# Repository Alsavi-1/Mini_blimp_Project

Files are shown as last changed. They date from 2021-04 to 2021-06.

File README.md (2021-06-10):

# Mini_blimp_Project
ECE412/ECE413 PSU Capstone 2021
CoppeliaSim 
  - Blimp simulation file
  - Tutorial for CppeliaSim itself
Main Document
  * 412 Document
    - Research/work done during (Winter term 2021)
  * 413 Document
    - Research/work done during (Sprin term 2021)
  * Full BOM Assembly
    - 3D solid works part for Gondola
    - Contains materials to build gondola
  * Full Blimp Analysis
    - 3D solid works part for Gondola
    - Contains materials to build gondola
  - 
  -
  -
  -
  -
Meeting minutes
  - Thursday Meetings with Ethan
Research Readings
  - Research papers involving blimps
    - Not used Papers (Research papers that weren't applicable)
    - Used Papers (Applicable information involving blimps)
WPR (Weekly Progress Reports)
  - Each date contains the current work done that week and what is going to be done the next

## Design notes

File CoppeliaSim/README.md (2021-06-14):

The simulation file in this directory was developed with CoppeliaSim V4.1.0 (rev. 1).\
The current version of CoppeliaSim (as of the submission of this project) is V4.2.0 (rev. 5).\
Previous versions of CoppeliaSim may be found at:\
   https://www.coppeliarobotics.com/previousVersions

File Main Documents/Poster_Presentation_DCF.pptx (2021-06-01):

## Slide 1

Development of an Autonomous Blimp

Ben Vu, Dylan Filkins, Jacob Thomas, Nick Short, Victor Albarran, Zeming Zhou

Portland State University and Galois Inc

INTRODUCTION:

The growing applications of unmanned aerial vehicles (UAV) allows for cross industry benefits. One such UAV that could see large potential in these industries are blimps. These light than air vehicles provide a large range of capabilities due to their stability and energy consumption.
Galois Inc. proposed a project in which they could use a blimp within their office environment to relay messages to coworkers and have messages forwarded. Galois Inc. saw this a benefit to communicating in the office environment in an entertaining manner.
The joint venture between the electrical and mechanical engineering departments at Portland State University collaborated to develop a simulated blimp to iteratively analyze computer aided design (CAD) models. The design process was to look at different use cases for Galois Inc. and to determine the best configuration.
*Due to the COVID-19 pandemic, the scope and possibility of constructing a physical prototype was not possible.

OBJECTIVE:

software uses a 3D model of the blimp in addition to statistics about the blimp such as mass, buoyancy and maximum thrust to simulate the blimp moving within 3D space.
Navigation proved to be particularly difficult due to the lack of wheels or airfoils binding the velocity and heading of the blimp together. Instead, other methods were employed to recreate the forces normally provided by those features.
By oversteering through the turn, the thrust of the blimp can be used to redirect the velocity of the blimp to follow the desired curve.

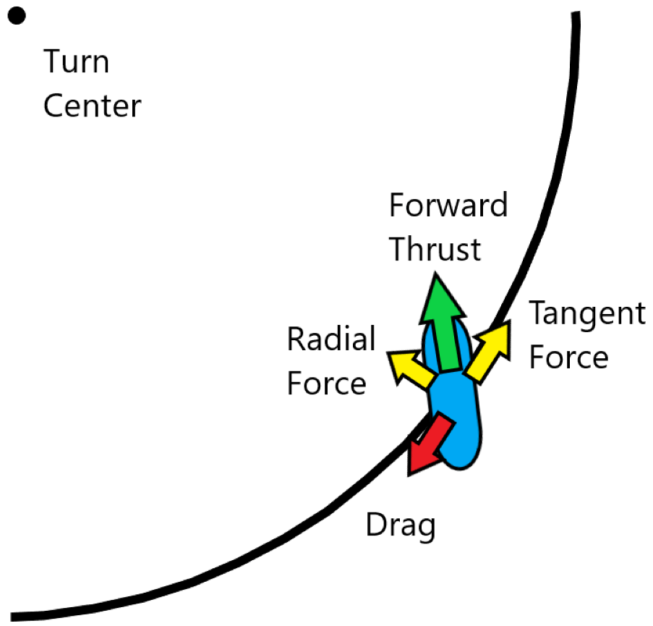
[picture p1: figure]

Chassis:
As part of a valuable deliverable for the sponsor a CAD design was developed to be used together with simulations. The basis of this was to be efficient with the limited time that the capstone had to evolve the simulation and design. Additionally, the simulation could provide more insights into how the chassis design would interact with the surrounding environment.
Only one chassis design was implemented due difficulties with the COVID-19 pandemic and sponsor’s interest

The chassis and the full-scale model is illustrated below in Figure 1 & 2. The CAD design was evaluated for pressure and velocity drop across the system ( Figure 3 & 4).

consideration the defined criteria of Galois Inc. in regards to modularity, manufacturability, and protection of electrical components.
It is suggested that future evolutions are made with the combination of simulations and CAD to further refine the project. All deliverables and documentation was passed onto Galois Inc. to provide a foundation of knowledge for the next version.

REFERENCES:

- Tao, Qiuyang & Tan, Tun & Cha, Jaeseok & Yuan, Ye & Zhang, Fumin. (2020). Modeling and Control of Swing Oscillation of Underactuated Indoor Miniature Autonomous Blimps. Unmanned Systems. 09. 10.1142/S2301385021500060.
- Jinjun Rao, et al. “A Flight Control and Navigation System of a Small Size Unmanned Airship.” IEEE International Conference Mechatronics and Automation, 2005, July 2005, doi:10.1109/icma.2005.1626776.
- Zufferey, Jean Christophe et al. “Flying over the Reality Gap: From Simulated to Real Indoor Airships.” Autonomous Robots 21.3 (2006): 243–254. Autonomous Robots. Web.
- Zheng, Zewei, Huo, Wei, & Wu, Zhe. (2013). Autonomous airship path following control: Theory and experiments. Control Engineering Practice, 21(6), 769–788.
- Ko, Jonathan et al. “Gaussian Processes and Reinforcement Learning for Identification and Control of an Autonomous Blimp.” Proceedings - IEEE International Conference on Robotics and Automation. N.p., 2007. 742–747. Proceedings - IEEE International Conference on Robotics and Automation. Web.
- Alsayed, Ahmad, and Eric Lanteigne. “Experimental Pitch Control of an Unmanned Airship with Sliding Ballast.” 2017 International Conference on Unmanned Aircraft Systems (ICUAS), 2017, doi:10.1109/icuas.2017.7991326.

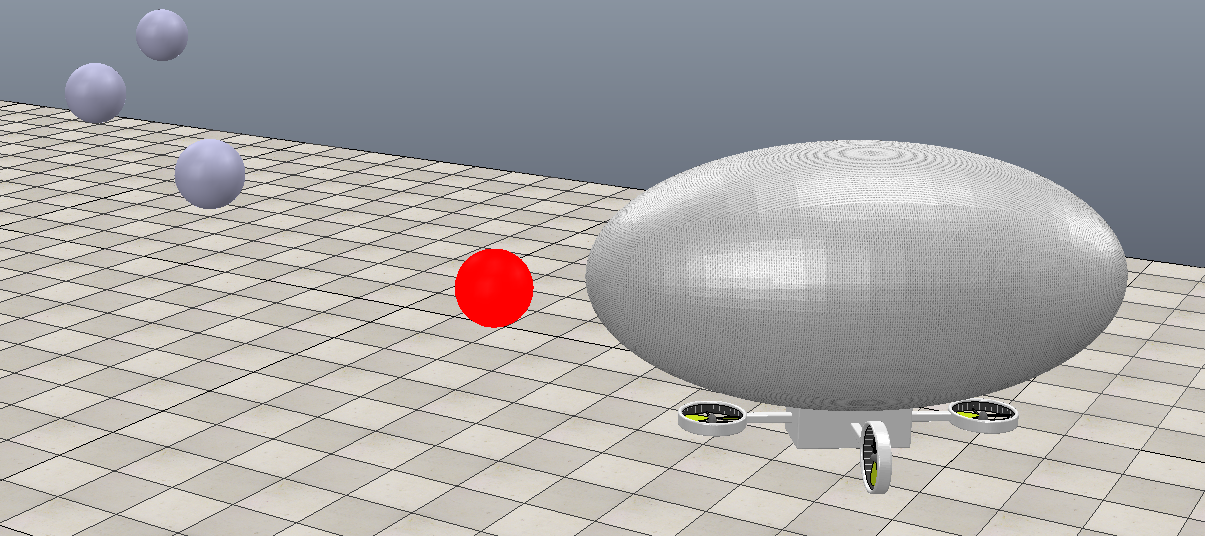
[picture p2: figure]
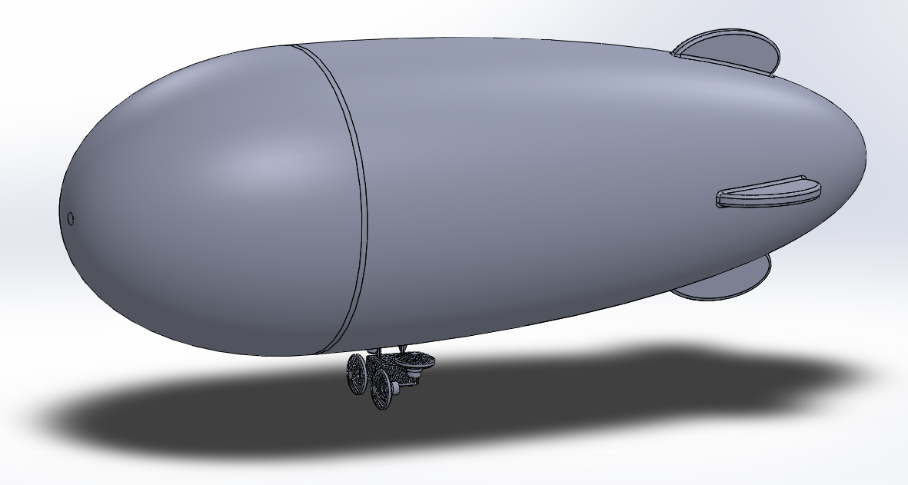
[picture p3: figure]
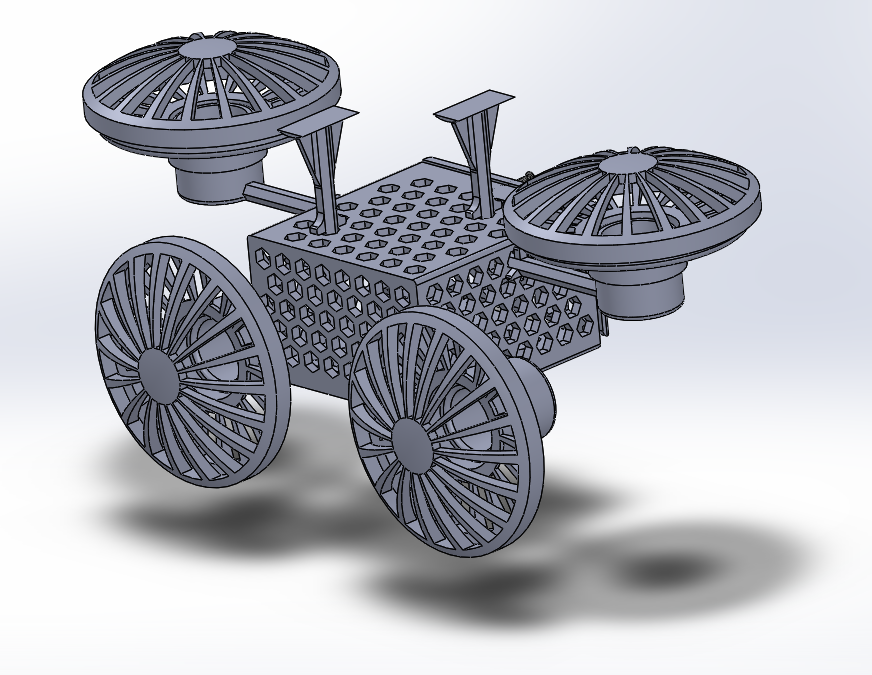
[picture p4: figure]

Figure 1: Full scale CAD model (left) and Figure 2: chassis design (right)

Figure 3 and 4: Illustrating aerodynamics of CAD model in regards to velocity and pressure changes.

CONCLUSIONS:

The pass off of knowledge and deliverables were completed to Galoic Inc. and Portland State University to a satisfactory level. The team was able to successfully develop several simulations in the programs of CopelliaSim and WeBots to start to look at different use cases for the sponsor. Within these simulations, we were able to model a blimp to follow a path of different waypoints and to define the outside factors affecting the blimps directional path.
A refined three dimensional CAD model was produced for these simulations to see the interactions. The model considered different engineering analysis of strength, material, and aerodynamics that could affect life cycle of the chassis. The CAD model also took into consideration the defined criteria of Galois Inc. in regards to modularity, manufacturability, and protection of electrical components. he CAD model also took into

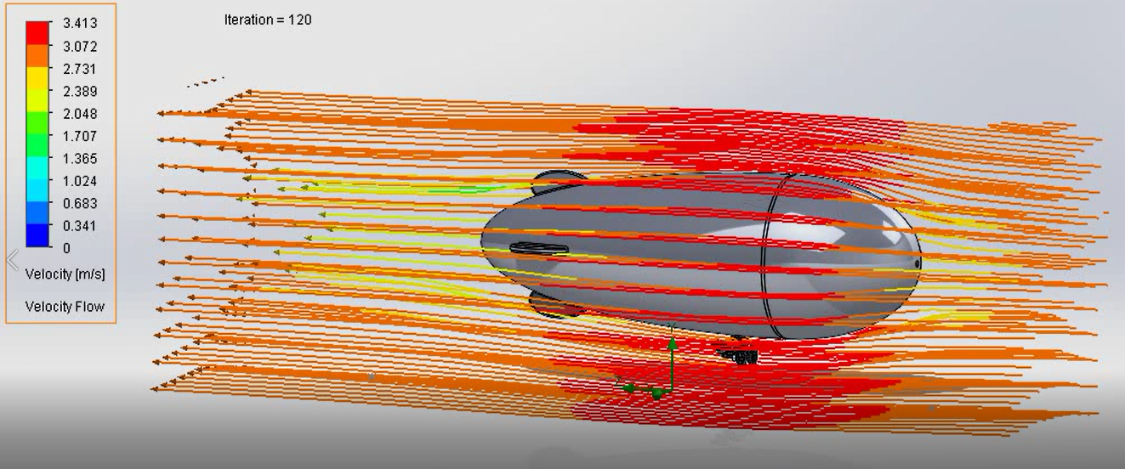
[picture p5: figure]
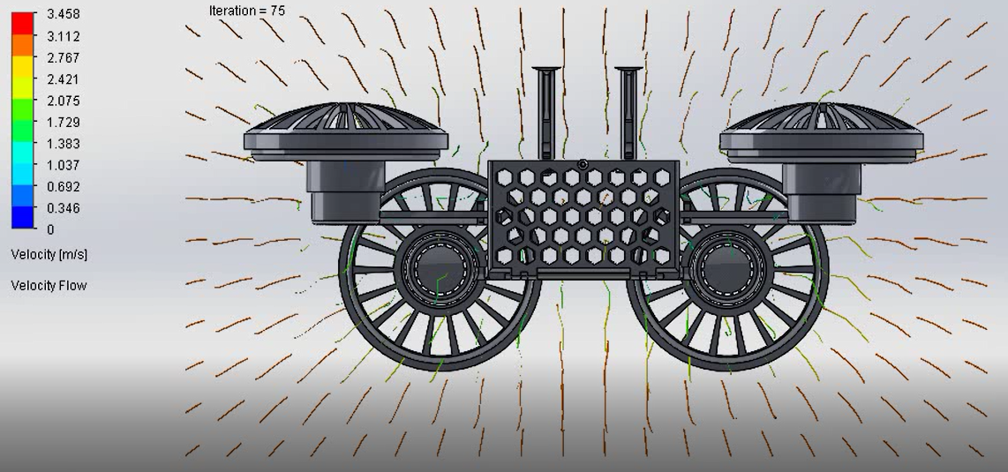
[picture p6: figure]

Create a simulation of a blimp and use the simulation to learn how blimps move, and create a chassis which can be used as a blimp gondola.

RESULTS:

Simulations:
Because meeting in person was not an option, a physics simulation was employed to model the dynamics of a blimp. This gave the opportunity to visualise blimp movement and investigate navigation methods. Two softwares were used: CoppeliaSim and WeBots. Each

ACKNOWLEDGEMENTS:

Special thanks for Galois Inc for sponsoring the capstone project and furthering our education through their support and dedication.
We thank professor Dr. Mark Faust for the constant assistance throughout the capstone project as well, as the electrical engineering insights to further develop our project.
We are appreciative for Dr. Marek Perkowski and Dr. Jun Jiao for their commitment in propelling our understanding of engineering topics. Through their inquisitive questions and presenting subject matter.

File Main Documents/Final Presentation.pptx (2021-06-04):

## Autonomous Mini Blimp

Team 4:
Ben Vu, Dylan Filkins, Jacob Thomas, Nick Short, Victor Albarran, Zeming Zhou
Sponsor: Galois Advisor: Marek Perkowski

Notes: Hello, this is team 4’s autonomous mini blimp project
Our sponsor is Golois and advisor is Dr. Perkowski
I’m Ben

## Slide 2

## Concept of Operations

Initial task
- Create a mini-blimp with some autonomous controls
- Is able to be manually controlled (similar to RC flight) by user
Now the task is to find simulation software that can validate blimp design
- Test different blimp designs (Volume, Shape, # of propellers)
- Simulate blimp performance
- Be able to output speed and turning capabilities of blimp

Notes: Original Concept of Operations
1 Concept of Operations
The purpose of this project is to design a proof of concept of a semi-autonomous blimp
that will fly around an office space which is our Minimum Viable Product (MVP). The
craft uses helium as its primary lift mechanism, the craft must be remotely operable by a
typical hobby controller, and all power sources, radios, sensor control systems are
subject to a weight restriction depending on the blimp helium and shape. Manual control
from a remote will allow the user six-degrees of freedom. Galois will use the final
designed blimp to be used in an office environment for various tasks and for a team
competition between blimps.

Ben 1

At the start, the idea was to create a mini-blimp with some autonomous controls
Which would be collision detection
But for the most part is user controlled with a hobby controller
That was a big promise and would prove to go beyond 2 terms
Now we revised the plan to use a simulation software to validate blimp design
The software will be able to test various designs (such as, size, shape, # of propellers)
And that will be used to simulate its performance
Then outputs its speed and turning capabilities

## Initial Plan

- The initial plan was to develop an autonomous blimp prototype for two scenarios (office use for Galois and DARPA competition).
- The office environment would be to relay information and messages to employees.
- The DARPA competition required the blimp to perform in a Quidditch like match to showcase capabilities
- Considerations by Galois and DARPA would be considered for autonomous operating and outside influences (wind, image recognition, attacks, etc)

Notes: Dylan:

As mentioned earlier

## Revised Plan

- Due to COVID-19 impacts the scope of the project was changed to focus efforts on office use.
- AI would be integrated later by the sponsor
- Creating a physical prototype was determined to be unfeasible. Instead a computer simulation would be created
- The simulation would model the behavior of a blimp to provide information about blimp dynamics
- The simulation could then be used to help design a custom chassis

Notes: Jacob 1

## The Main Components of the Blimp

- Envelope - It consists of a shell containing a gas less dense than air. The gas not only provides lift for the airship, but also provides a "structure" for the envelope to keep the shape of the shell unchanged.
- Gondola - It is used to carry various electronic equipment and as the connection point of the engine. The gondola is the heaviest part of the airship, so the lightest materials must be selected to manufacture the gondola.

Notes: zeming:

## Diagram

- Chassis Specifications:
  - ~ 22 x 10 x 8.5 cm
  - 80 grams without components
  - PLA
- Chassis Considerations:
  - Airflow over electrical components
  - Shroud over propellers
  - Protection of electrical components
  - Modularity in propeller placement

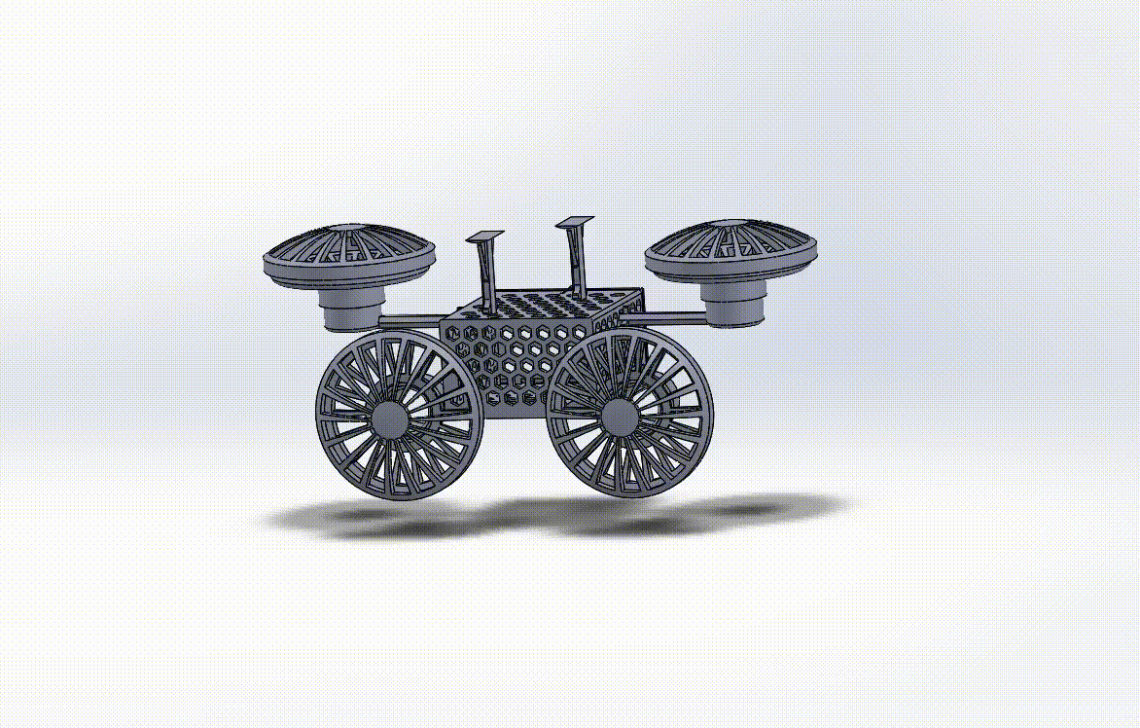
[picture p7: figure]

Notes: Dylan 2:

The diagram was an additional deliverable that was to be implemented along with the simulation. This was to allow concurrent development of the design and simulation. This allowed a proper efficiency of time and gain greater insight into the effect of the chassis design.

So you can see the design in the full scale with a respective size of 1.4 m. If we look at the two photos below, we will see the chassis design that was design. As well as the exploded view of the design with all fasteners.

The chassis design was further analyzed with the material properties and looking at the sponsor’s desires.

## Overview of Software

- Several softwares were considered for use
- Each software was ranked based on features which were considered to be important
  - Physics Modeling
  - Ability to calculate path deviation
  - Ability to visualize simulation
- Two softwares were chosen to create simulations:

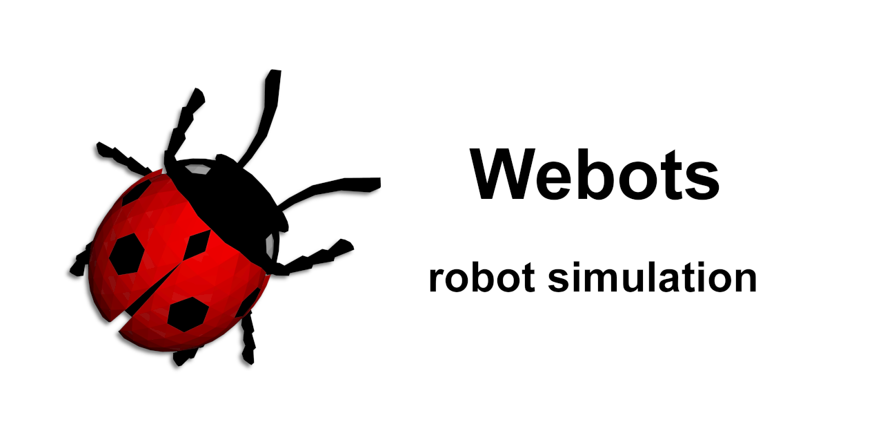
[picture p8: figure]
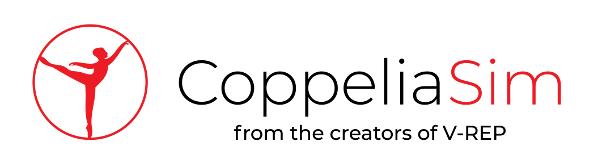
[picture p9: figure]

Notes: Jacob 2

## CoppelliaSim

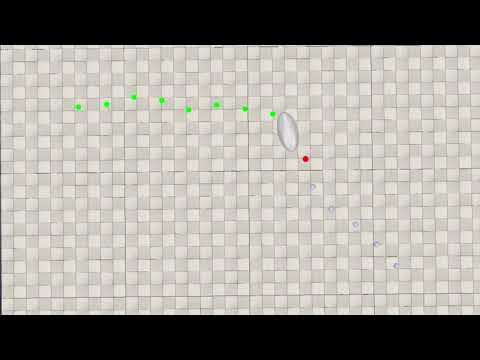
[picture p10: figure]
CoppeliaSim Simulation of a blimp with primitive way point navigation.

- Open source and multi-platform desktop application
- Built-in library includes robots, sensors, and actuators.
- Simulation scripts are natively written in LUA.
- Remote API access via C++, Java, Python, Matlab, and LUA.
- Several options for physics engines, including Bullet, ODE, Vortex, and Newton.
- Runs on Windows, Linux and macOS.

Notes: Nick 2

## WeBots

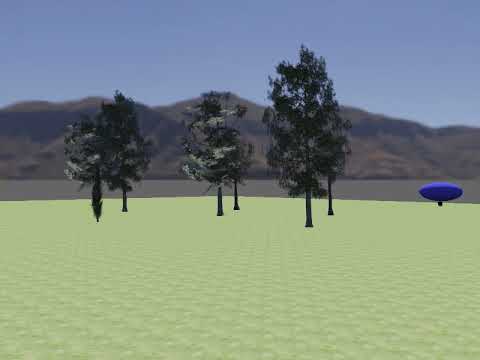
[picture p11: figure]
ECE413 Blimp Simulation

- Open source and multi-platform desktop application
- Library includes robots, sensors, actuators, objects (https://cyberbotics.com/doc/guide/objects) and materials (https://cyberbotics.com/doc/guide/appearances).
- Simple AP (https://cyberbotics.com/doc/reference/nodes-and-api-functions)I and can be programmed in C (https://cyberbotics.com/doc/guide/using-c), C++ (https://cyberbotics.com/doc/guide/using-cpp), Python (https://cyberbotics.com/doc/guide/using-python), Java (https://cyberbotics.com/doc/guide/using-java), MATLAB (https://cyberbotics.com/doc/guide/using-matlab).
- Modern GUI, a physics engine and an OpenGL 3.3 rendering engine.
- Runs on Windows, Linux and macOS.
Webots Blimp Simulation (https://youtu.be/IY3bQu2_xho)

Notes: Victor 2

Open source and multi-platform desktop application
Library includes robots, sensors, actuators, objects and materials.
Simple API and can be programmed in C, C++, Python, Java, MATLAB.
Modern GUI, a physics engine and an OpenGL 3.3 rendering engine.
Runs on Windows, Linux and MacOS

## What was Achieved

- Airship - The envelope design allows navigation through indoor environments.
- Gondola - The gondola uses a lightweight perforated design so the air resistance is not significant and will not reduce the top speed of the blimp. This model also does not negatively affect the balance of the blimp.
- Blimp Movement - We have theorized an optimal movement method but were not able to implement it into the simulation.

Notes: Zeming 2

## Post Mortem

- Uncertain deliverables due to miscommunication which lead to poor use of time.
- Team identified that project was falling behind schedule and requested assistance.
- Team members had very little experience with simulations and had a difficult time transitioning to the new approach.
- The simulation turned out to be an effective tool but would have been more successful if it had been the initial method.

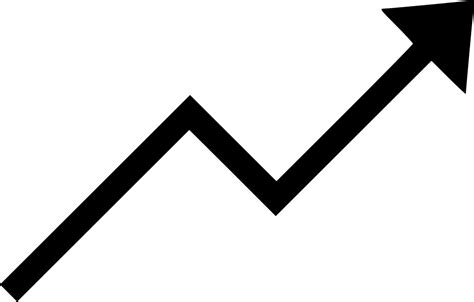
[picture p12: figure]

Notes: Ben 2
At the start, we were given a scope that was very broad
We narrowed down our scope by pursuing an experimental approach
This turned out to be the wrong direction
To correct this we redirected our project to pursue a digital simulation
However the team had little experience with the simulation software which made this transition difficult
Considering how effective the tool turned out to be, the team would have been more successful if this was the first approach

## Contributions

Ben Vu - Documentation, SolidWorks, Github
Dylan Filkins - SolidWorks, Documentation
Jacob Thomas - Documentation, Simulation
Nick Short - Simulation, Documentation
Victor Albarran - Simulation, Github, Documentation
Zeming Zhou - Simulation, Documentation

## Questions?

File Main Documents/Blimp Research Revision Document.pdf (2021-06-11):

# Autonomous Blimp Modeling: A Feasibility Study and Annotated Bibliography

Authors:
Jacob Thomas
Nick Short
Dylan Filkins
Victor Albarran
Zeming Zhou
Benjamin Vu

ECE 412
Portland State University

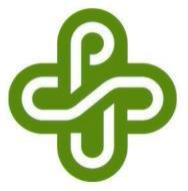
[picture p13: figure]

Revision 3.2
Date:06/08/2021

### Autonomous Blimp Modeling

# Table of contents

1. Executive Summary | 4
2. Introduction | 5
2.1 Project Constraints | 6
3. Design Space | 6
3.1 Blimp Design Space | 7
3.2 Blimp Performance Characteristics | 8
3.3 Metrics | 10
3.4 Blimp Control Space | 11
3.5 Blimp Design Goals | 12
4. Simulation Software Analysis | 13
4.1 Evaluation Metrics | 13
4.2 Software Evaluation | 17
Physics Abstraction Layer | 17
Simulink | 18
CoppeliaSim | 19
Vortex Studio | 20
RoboLogix | 21
SimulationX | 22
Webots | 23
Gazebo | 24
EZPhysics | 25
4.3 Primary Software: CopelliaSim | 26
4.4 Secondary Software: WeBots | 26
5. Software Implementation | 27
5.1 Maneuverability | 27
5.2 Turning Method | 27
6. Component Analysis | 30
6.1 Envelope | 30
6.2 Chassis | 31
6.2.1 Overall Design | 31
6.2.2 Modularity | 32
6.2.3 Aerodynamics: | 32
6.2.4 Mass | 34
6.2.5 Future Design Considerations | 35

6.3 Motors | 35
5.4 Props | 36
6.5 Batteries | 36
7. Conclusion | 37
8. Works Cited | 39
9. Table of Figures | 39
10. Annotated Bibliography | 40
Revisions | 49

## 1. Executive Summary

This project was completed for the engineering department of Portland State University and Galois Inc for certification of a bachelor degree. The purpose of the project was to investigate the potential use cases for Galois Inc. pertaining to an autonomously operated blimp in an office environment and for a DARPA competition. The results of the project were a collection of deliverables for Galois. Including running simulations in CopelliaSim and Webots, 3D CAD work of a potential gondola, coding scripts, and an annotated bibliography. These deliverables are to assist Galois in the future development of an autonomous blimp for the stated purposes.

## 2. Introduction

Blimps are classified as non-rigid airships and lighter-than-air (LTA) vehicles. They consist of an envelope containing a gas that is less dense than air. The gas provides both lift and a form for the blimp. Since blimps are non-rigid, they have no internal or external structure to maintain the shape of the envelope, as in rigid and semi-rigid airships.

Blimps usually have a small section, specified as a gondola (commonly attached to the bottom of the blimp), that carries people and equipment and serves as an attachment point for engines. The gondola is often one of only two fixed parts of a blimp—the other being the tail fins.

As the blimp’s elevation increases during flight, the gas inside the envelope expands. Since blimps are generally overinflated, there must be some mechanism to prevent the envelope from exploding due to gas expansion. Most blimps contain internal airbags or “ballonets” filled with air to counteract such inflation.

As the blimp rises, the expanding gas pushes on the ballonets, forcing air to escape and providing a volumetric space for the gas to expand freely. When the blimp loses altitude, exhaust from the engines is pumped into the ballonets, inflating them to fill the volume of the contracting gas, thus maintaining the pressure and shape of the envelope.

From a modern perspective, blimps did not exist before the 1900s. Up to that point, LTA vehicles consisted solely of hot-air balloons. Hot-air balloons were only capable of being controlled vertically.

From the 1920s to the 1950s, LTA vehicles were used as passenger transportation and for military purposes. Modern blimps, though, are functionally used for advertising and long-term surveying, such as whale research. The ability of a blimp to stay in the air for hours, or even days, makes it a preferred vehicle for tasks that require an extended operation.

The typical uses of modern blimps require envelopes that are massive in size. This allows for a payload capacity that is viable for carrying the equipment and personnel required. This project is the result of a non-standard need. The blimp designed in this project will be used entirely indoors, in an office environment, performing “surveillance”, and in a warehouse environment, playing a variation of the sport Quidditch from the

Harry Potter novels. There are few examples of such small-scale, unmanned blimps deployed indoors to draw upon.

The blimp will need to navigate narrow hallways and open spaces contending with air currents and obstacles. It will be required to maintain a position within a certain distance of a target location, as well as be maneuverable enough to follow a flight path with a path deviation below a specified threshold. Eventually, the blimp should be part of an autonomous system, so it will need network connectivity and the ability to identify objects. This is most likely accomplished with a camera and some image processing capabilities. Additionally, the blimp may need to identify individuals that it cannot directly see. This could be done with a microphone and speech recognition algorithms.

## 2.1 Project Constraints

Due to the COVID pandemic and constraints on face-to-face meetings, your project focus has changed from creating a physical prototype to a feasibility study on autonomous blimps in an office and competition environments. The major reason for this change is because of the difficulty in constructing a physical model and keeping safety protocols. This feasibility study hopes to be a guide for others to develop a prototype based on our simulated work.

## 3. Design Space

Design Space Exploration (DSE) refers to the activity of exploring design ideas or alternatives prior to implementation or application. DSE is useful for many engineering tasks since it operates on the potential candidates of design. A trade-off analysis between each of the implementation options based on a certain parameter of interest forms the basis of DSE. The parameter of interest could vary across systems, but the commonly used parameters are power, performance, and cost. Additional factors like size, shape, weight, etc. These factors don’t change for a blimp. The primary application will be indoors in an office building. Factors such as size, shape, and weight now have limitations due to standard door size, narrow hallways, and stairways.

## 3.1 Blimp Design Space

The listed parameters define a simplistic designated design space for the blimp’s performance criteria.
- Size
- The main location of the blimp will be indoors in an office space where its maximum size is limited to ceiling height and doorway width of location.
- Shape
- It will need to accommodate a gondola, be able to fit standard doors and narrow stairways.
- Volume
- The total space the helium will occupy in the envelope and this will determine minimum lift capability.
- Total Mass
- The mass of the envelope and the gondola together.
- Gondola Placement
- How it will be mounted to the envelope. Whether by adhesive or friction mount.
- Gondola Characteristics
- Material – High density 3D printable polymer.
- Machinability – Ideally one continuous piece.
- Modularity – Iterative placement of components.
- Propeller Characteristics (Ct - Pull coefficient, Cp-Power coefficient, D- propeller direct, n-propeller speed)
- Structural characteristics- It resists stretching of uneven forces in different directions and has good toughness.
- Pull Coefficient - C
T

=

T
ρn

2D

4

- Power Coefficient - C
| P

=

P
ρn

3D

5

- Propeller Efficiency - η
| prop

= J

C
T
C
p
- Battery
- The size of the battery is limited by the size of the blimp gondola.

- Envelope – Polyester Film PVC; PVC material elasticity, strong anti-aging ability and PVC material resistance to high temperature, shape is preserved at high temperatures.
- Gas– Helium
- Physical properties - The surface tension is very small so the envelope can be relatively weak. The gas density is 0.1786g/L. (0C, 1 atm)
- Computing Placement – The physical placement of the computing components of the blimp.
- Electronic Control Units – A centralized Electronic Control Units can be placed on the gondola’s frame, or a data transmitter can be used to send data to an off-frame computer.
- Sensors – Need to be integrated into the blimp. Can be on the gondola.
- Motors – Also on the blimp. Optimal placement is determined by simulation.
- Servos – need to be placed on the blimp’s gondola/ frame

## 3.2 Blimp Performance Characteristics

Blimp performance is dependent on several characteristics. These characteristics can be modified to achieve desired performance.

Maximum Payload Weight
Payload weight is how much weight the blimp can carry. Greater payload weight allows for more sensors and a larger battery. Maximum Payload weight is affected by the buoyant force.

Maneuverability
Maneuverability is the bllimp’s ability to change position, direction, and speed. Blimp Maneuverability is affected by several factors:
- Mass (inversely proportional) – An increase in mass negatively impacts maneuverability by increasing the inertia needing to be overcome to effect a change in direction.
- Volume (inversely proportional) – Regardless of the shape, an increase in volume equates to an increase in the surface area, which increases overall air resistance.
- Shape – While some shapes may be great for forward motion, the surface area seen perpendicular to other axes is generally greater, increasing the air resistance in those directions. A spherical balloon shape is the most universally maneuverable shape.

- Thrust (proportional) – Different from the speed characteristic, the thrust parameter (regarding maneuverability) is related to the direction of the thrust more so than its amplitude.

Sensing
The tasks that a blimp performs largely dictate the sensors required to operate. A simple radio controlled blimp needs no sensing to be controlled by the user, though some sort of object detection is handy to avoid collisions. A more complex, autonomous or semi-autonomous blimp will certainly need more sensors to operate. Tasks such as localization, object avoidance, and object detection all require disparate sensing solutions, with a small amount of overlap existing between some tasks.

It would be sensible to divide sensors into categories related to their applications, and beneficial to include sensors in multiple categories, where appropriate. This will allow an informed decider to potentially minimize the number of sensors needed to perform all the required tasks. The following is a categorical list of different sensor solutions:

- Localization
- LiDAR – These sensors work in a similar fashion to RaDAR but using light instead of radio waves. They use “time of flight” to calculate distance. By firing a laser pulse, then measuring the time for the pulse to reach an object, be reflected, and return, the LiDAR can calculate the distance to the object (using the constant, C).
- GPS – These sensors operate on the principle of trilateration. Each GPS satellite broadcasts their location with a timestamp. When the GPS sensor can receive signals from four satellites, it can use trilateration to calculate its precise location relative to the satellites, as well as calculate a very accurate time (GPS satellites utilize atomic clocks to generate their timestamps).
- Accelerometers – Accelerometers measure the acceleration experienced by the accelerometer. These measurements can be used to estimate distance traveled, though not very accurately.
- Object Avoidance
- LiDAR – Operates as above. Can be used to detect the existence of, and distance to, new objects around the blimp. Because this sensor is also used with localization, it makes a good choice, as it can simplify a sensing system and lower the impact on the control logic.
- IR proximity – These sensors are single point detectors that often only detect the existence of an object in their range, but can sometimes communicate distance.
- Ultrasonic Rangefinder – These sensors use a “time of flight” method, similar to LiDAR and IR proximity sensors to calculate the distance to an object. Rather than using light, they use high frequency sound waves. The consequence of this is that they are most accurate when the density of the surrounding air is known. This necessitates the use of a barometric pressure sensor and a temperature sensor in conjunction with the ultrasonic rangefinder. This may be impractical when compared with IR proximity sensors or LiDAR modules.
- Object Detection
- Cameras – A digital image can be used for object recognition, as well as navigation. Images or a video feed can also be transmitted to a user to see from the blimp’s perspective.
- Microphones – Measure sound which can be used for speech recognition. This is object detection, if humans are considered objects to be detected. In the event that a person is not in the field of view of the camera, their presence in a room could still be detected.
- Diagnostics
- Ammeters – Simple devices which measure current. This can be implemented with a precision one ohm (or less) resistor and an analog to digital converter (ADC) with a precision reference voltage (an IC voltage reference such as a 7805 may be sufficient). The resistor is put into the current path and the ADC measures the voltage across the resistor against the reference voltage. The current through the resistor–and through the circuit–can be calculated from this measurement with little impact on the circuit. Care must be taken to ensure that the current draw being measured will never exceed the capacity of the resistor.

It’s important to note that oftentimes, one sensor alone is not enough to perform a task. For example, using an accelerometer to keep track of position is possible, but not very accurate, as the error compounds during the math required to calculate position. In this case, it would be prudent to include GPS or LiDAR as an occasional “sanity check”.

Flight Time
Flight time is how long the blimp can run and maintain an altitude. Blimp Flight time is affected by several factors:
- Passive lift (lift from helium; proportional) – Passive lift increases airtime, but only as it approaches being balanced against the mass of the blimp. As the balance shifts one way or the other, thrust must be applied in greater amounts to keep the blimp afloat.
- Battery capacity (proportional) – Larger battery capacity increases the time that thrust can be applied, at the cost of mass.
- Current draw (inversely proportional) – With no change in battery capacity, decreasing current draw will increase the airtime, as the battery will be able to supply current for a longer period of time.

## 3.3 Metrics

Blimp characteristics are measured and compared using several metrics: top speed, turning radius, acceleration, total mass, buoyant force, and power draw. Some of these metrics can be measured directly using onboard instruments, while others must be calculated experimentally.

Top Speed is measured by flying the blimp between two points and measuring the time the blimp takes to travel. The blimp should begin traveling before reaching the first point and continue after the last point to ensure top speed is maintained between the points. A higher top speed will allow the blimp to travel distances faster. Top speed is measured in meters per second (m/s).

Turning Radius is measured by flying the blimp in as tight a circle as possible and then measuring the radius of the circular path. Blimps employing a motor couple moment for yaw articulation will have a turning radius of zero. The turning radius is measured in millimeters (mm).

Acceleration is measured with an accelerometer attached to the blimp. It affects how quickly the blimp can reach its top speed. A greater acceleration will achieve top speed faster. Acceleration is measured in meters per second squared (m/s²
).

Total Mass is measured using a digital scale or balance. A blimp with more mass will accelerate slower and require more helium to stay afloat. Every component added to the blimp will increase its total mass. The total mass measured in kilograms (kg).

Buoyant Force is calculated using the blimp’s helium volume. If this force is greater than the force of gravity, the blimp will rise, and if it is less than the force of gravity, the blimp will fall. The buoyant force is measured in Newton (N).

Power Draw is measured by a digital multimeter. Amp draw will be measured and the total voltage is calculated by the total components used. The product of both will be the total wattage (W).

Since the blimp will be simulated using a physics simulation software, none of the metrics will need to be measured. Instead, some of the metrics can be calculated and displayed for easy viewing.

## 3.4 Blimp Control Space

Achieving as many degrees of motion as possible will provide the greatest control of the blimp. There are six degrees of movement which are separated into three directions: forward/backward, left/right, up/down. Each direction has a translational component and a rotational component. If an aircraft points in the positive x-direction, the rotational components of the x, y, and z axes are referred to as roll, pitch, and yaw respectively.

The blimp’s control space is determined by the number of control inputs it has. These inputs will either create thrust in a certain direction or will change the direction of the thrust of one or more thrust inputs. These inputs can be referred to as Force Control Inputs (FCIs) or Vectoring Control Inputs (VCIs). These inputs can be configured in several ways to achieve control within desired axes of movement.
Due to the location of the gondola below the envelope, the center of mass is located below the center of lift of the blimp. These properties cause the blimp to return to this orientation after being perturbed. Thus, roll and pitch rotation are not sustained without an active force input. This property is beneficial to a blimp, because sensors located on the gondola may depend on a stable orientation to perform optimally. Because of this, achieving roll and pitch control is not desirable for a blimp.

The optimal control input configuration includes three FCIs. One is oriented vertically below the blimp’s center of mass. This control input will be running whenever the blimp is on to counteract the buoyant force of the blimp. It will also change intensity to control altitude. The other two FCIs are oriented horizontally, parallel to each other, and facing aft. These two inputs are offset from the center of the blimp in order to create a couple of moments about the blimps Z-axis. Setting the input’s intensity equal to one another moves the blimp forward or backward. Likewise, by setting the inputs to separate intensities, yaw articulation can be achieved.

## 3.5 Blimp Design Goals

Ideally, a blimp design would be simultaneously fast, maneuverable, and be able to stay in the air for a long time. Realistically, each of our characteristics comes with tradeoffs with respect to each other. For example, increasing the airtime by increasing the battery capacity will undoubtedly increase the mass, which would result in worse maneuverability. Increasing speed (by increasing the thrust) would lower airtime (by increasing current draw).

Since the design characteristics are—while not exactly mutually exclusive—somewhat incompatible, it becomes important to decide which of the characteristics are most important. Perhaps a slow and long-lived, but highly maneuverable blimp is desired. It may be that the goal to be achieved is a blimp that can maintain a position, very accurately, for a long period of time.

## 4. Simulation Software Analysis

The main goal of a blimp simulation is to validate mathematical models of alternative blimp designs, provide visual representations of them and our sponsor can continue the research project of the blimp. The simulation software will provide control of the inputs, modification of the dimensions, and the ability to model a blimp.
The performance of the blimp will be simulated through different scenarios and by changing the values of the variables. Performance characteristics that we will include are weight load, maneuverability, sensor awareness, and flight time. This performance characteristic will be obtained by changing the input and model of the blimp. Metrics will be obtained by comparing the performance characteristics, the metrics we would like to obtain are speed, acceleration, turning radius, power (if simulation allows it), buoyant force. It is also important for the simulation to be open source or have a free student license.

The criteria for the decision matrix have been determined based upon the importance of a particular option or characteristic that would be expected in simulation software. The criteria are either a “true/false” criteria, or a scored criteria, from one (1) to five (5). A value of two (2) or four (4) represents an option or characteristic whose performance is better than the previous value, but not quite as good as the next.

## 4.1 Evaluation Metrics

Has Student Licence
Since it is not feasible to purchase all simulation softwares for evaluation, it is important for a software to be available for experimentation. In order to choose an expensive software, it must be a clear contender for best software. Software which is free can be used and evaluated without investment so this metric will be weighted at 5.
- 0 - Licence required
- 5 - Student licence or open source

Blimp Physics Modeling Ability Modeling blimp physics is crucial for a blimp modeling simulation. This metric will be weighted at 5.

- 1 - Basic simulation only evaluates one _
- 3 - Simulates general physics with possibility for a blimp to be simulated

- 5 - Software tailor made for aircraft/robot simulation

Ability to Modify Blimp Dimensions Modifying blimp dimensions allows for quick changes to components within the simulation. This allows the AI developer to quickly implement hardware changes and update AI accordingly. This metric is weighted at a 2.

- 1 - Blimp dimensions not simulated
- 3 - Blimp model fixed once imported from separate software
- 5 - Blimp dimensions and density can be changed from within software

Ability to Modify Control Inputs Modifying control inputs allows AI developers to experiment with different force input configurations. This allows more freedom in AI development if it is decided that a less efficient control configuration is easier to develop for. This metric will be weighted at 3.

- 1 - No control modification, control inputs are fixed to model
- 3 - Control inputs can be modified with much effort
- 5 - Control inputs easily modified

Ability to Calculate Power Usage Measuring power used by the blimp is an important capability of the simulation software. The blimp will only be able to run as long as its batteries will allow, so in order to choose a battery which will offer the power needs of the blimp, while not weighing the blimp too much, an accurate calculation of power usage is required. This is a simple calculation for a computer, but tedious to do by hand and important to blimp development so it will be weighted at 4.

- 1 - software only calculates time length and users will need to calculate power usage with known average power draw of components
- 3 - software calculates power draw of components over time but does not calculate total power usage
- 5 - software calculates total power usage over time.

Ability to Measure Flight Path Deviation Deviation from the intended flight path is a useful way to evaluate the effectiveness of a blimp’s AI controller. A larger deviation indicates a less effective controller. Since this metric is crucial for the evaluation and development of AI, it will be weighted at 4.

- 1 - No flight path information

- 3 - Raw data points of flight path provided which can be compared to intended flight path
- 5 - Flight deviation calculated and provided

Ability to Visualize Simulation Visualizing the simulation is not critical for AI development, but it can make troubleshooting easier by allowing programmers to see decisions made by an AI as they are made. This metric will be weighted at a 2.

- 1 - No visual information
- 3 - Some blimp representation but no physics simulator
- 5 - Full blimp physics simulator

Has Common Scripting Language Having a common scripting language will make AI integration much easier and allow development without the need to learn a new programming language. Since the sponsor is technically savvy and willing to work with the simulation’s back end, this metric will be weighted at 3.

- 1 - Proprietary language
- 3 - Uncommon language
- 5 - Common language

Table 1: Simulation Software Decision Matrix (Higher Score is Better)

Software Name (Multiplier) | Has Free/Student Licence (5) | Blimp Physics Modeling Ability (5) | Ability to modify dimensions (2) | Ability to modify control inputs (3) | Ability to calculate power usage (4) | Ability to measure path deviation (4) | Ability to visualize simulation (2) | Has common scripting language (3) | Total
Physics Abstraction Layer (http://www.adrianboeing.com/pal/index.html) | 5 | 3 | 4 | 3 | 2 | 4 | 1 | C++ 5 | 98
Matlab w/Simulink (https://www.mathworks.com/help/simulink/) | 5 | 1 | 2 | 3 | 2 | 4 | 1 | Matlab 5 | 84
CoppeliaSim (https://www.coppeliarobotics.com/) | 5 | 4 | 5 | 5 | 2 | 4 | 5 | C/C++, LUA 5 | 119
Vortex Studio (https://www.cm-labs.com/vortex-studio/) | 0 | 5 | 5 | 5 | 2 | 2 | 5 | 3D modeling GUI 1 | 79
RoboLogix (https://robologix.com/) | 0 | 3 | 4 | 3 | 2 | 1 | 5 | Unique modeling 1 | 67
SimulationX (https://www.esi-group.com/products/system-simulation) | 0 | 3 | 1 | 5 | 5 | 5 | 1 | Custom Flowchart 2 | 82
Webots: robot simulator (https://cyberbotics.com/#features) | 5 | 5 | 4 | 3 | 2 | 2 | 5 | C, C++, Python, Matlab 5 | 108
Gazebo simulator (http://gazebosim.org/) | 5 | 3 | 3 | 3 | 2 | 2 | 4 | Unique modeling, run in linux 2 | 90
ezphysics (http://ezphysics.org/joomla/) | 5 | 1 | 2 | 3 | 1 | 2 | 3 | C++, Python,Matlab 5 | 76

## 4.2 Software Evaluation

Physics Abstraction Layer
PAL acts as an interface between several different physics engines and your own software. It has built-in functionality for rigid bodies, sensors, and actuators, as well as being able to. This would give us more control over things, but it would come with the added work of having to write a more heavy framework.

Has Student Licence

5 - Software is open source.

Blimp Physics Modeling Ability

3 - Has access to multiple physics engines, but nothing specific to blimps.

Ability to Modify Blimp Dimensions

4 - Dimensions can be changed in code, but it is ungainly.

Ability to Modify Control Inputs

3 - Control inputs can be modified, but need to be translated from PWM/voltage to force.

Ability to Calculate Power Usage

2 - No built-in functions for calculating power usage. Would require custom methods.

Ability to Measure Flight Path Deviation

4 - Deviation can be calculated, but only roughly, from time-sliced flight path estimate.

Ability to Visualize Simulation

1 - Has no visualization.

Has Common Scripting Language

5 - Compatible with multiple common languages.

Simulink
Simulink is a semi-graphical add-in for Matlab that allows the definition of individual components of a system. The components are linked together with defined interactions to create a simulation of the system. This would be a decent option, as Matlab is a robust language for solving problems that are defined by many equations.

Has Student Licence

5 - Has a student license.

Blimp Physics Modeling Ability

1 - No built in physics. This functionality would need to be written entirely.

Ability to Modify Blimp Dimensions

2 - Model cannot be imported and dimensions are “hard-coded”; difficult to change.

Ability to Modify Control Inputs

3 - Control inputs can be modified, but need to be translated from PWM/voltage to force.

Ability to Calculate Power Usage

2 - No built-in functions for calculating power usage. Would require custom methods.

Ability to Measure Flight Path Deviation

4 - Deviation can be calculated, but only roughly, from time-sliced flight path estimate.

Ability to Visualize Simulation

1 - Has no visualization.

Has Common Scripting Language

5 - Uses a common and well supported language.

CoppeliaSim
CoppeliaSim is graphical simulation software that allows the user to simulate rigid body physics in a visual way. It utilizes the ODE, Bullet, Vortex, and Newton physics libraries. Provides collision detection, distance calculation, and motion planning, among other functions. Plugins are programmed in C/C++, and the behavior of the simulator can be modified with LUA. Has built-in sensors and actuators and the ability to import 3D models from external software.

Has Student Licence

5 - Has a student license.

Blimp Physics Modeling Ability

4 - Solid physics engine with ability to import CAD models.

Ability to Modify Blimp Dimensions

5 - Dimensions, mass, moments of inertia, and other parameters are all modifiable.

Ability to Modify Control Inputs

5 - Can easily modify control inputs through code or GUI.

Ability to Calculate Power Usage

2 - No built-in functions for calculating power usage. Would require custom methods.

Ability to Measure Flight Path Deviation

4 - Deviation can be calculated, but only roughly, from time-sliced flight path estimation.

Ability to Visualize Simulation

5 - Simulation fully visualizable.

Has Common Scripting Language

5 - Compatible with multiple common languages.

Vortex Studio
Vortex Studio is a physics engine focusing on collision detection, and the way separate bodies interact with one another. It is primarily focused on vehicles and mobile robotics and includes a robust 3D modeling suite

Has Student Licence

0 - Does not have student licence

Blimp Physics Modeling Ability

5 - Physics simulator is designed to simulate mobile robots

Ability to Modify Blimp Dimensions

5 - Software has native modeling ability

Ability to Modify Control Inputs

5 - Control inputs are easily moved around blimp

Ability to Calculate Power Usage

2 - Measures time simulation is running

Ability to Measure Flight Path Deviation

2 - Tracks path of vehicle

Ability to Visualize Simulation

5 - Full physics modeling suite

Has Common Scripting Language

1 - Proprietary language

RoboLogix
RoboLogix is a software designed for modeling various types of robots. It has a physics engine which allows different models to interact with one another. Interaction with the robots occurs primarily with the RoboLogix Control Panel, a GUI modeled after a physical control panel. The various buttons on the panel can be tied to different actions of the robot being modeled.

Has Student Licence

0 - No student license

Blimp Physics Modeling Ability

3 - Some physics modeling but not intended for mobile robots

Ability to Modify Blimp Dimensions

4 - importable models

Ability to Modify Control Inputs

3 - Basic control input ability

Ability to Calculate Power Usage

2 - Simulation only keeps track of robot

Ability to Measure Flight Path Deviation

1 - not integrated

Ability to Visualize Simulation

5 - Full physics modeling

Has Common Scripting Language

1 - Unique Modeling

SimulationX
SimulationX focuses on the inner workings of a system. It has a GUI oriented toward modeling the individual components and how they react with one another. The software does not use a model, but instead creates graphs to show various metrics set by the user.

Has Student Licence

0 - Paid License

Blimp Physics Modeling Ability

3 - models certain aspects of blimps

Ability to Modify Blimp Dimensions

1 - No blimp model

Ability to Modify Control Inputs

5 - Control inputs added as flow chart boxes

Ability to Calculate Power Usage

5 - If simulation is designed to simulate power usage, calculation will be easy to use

Ability to Measure Flight Path Deviation

5 - good calculations if simulation is designed for this metric

Ability to Visualize Simulation

2 - Simulation IO is static flow chart and dynamic graphs

Has Common Scripting Language

2 - GUI Flowchart

Webots
Webots is an open-source graphical simulation software and multi-platform desktop application used to simulate robots. It provides a complete development environment to model, program, and simulate robots. Its library includes robots, (https://cyberbotics.com/doc/guide/robots) sensors, (https://cyberbotics.com/doc/guide/sensors) actuators, (https://cyberbotics.com/doc/guide/actuators) objects, (https://cyberbotics.com/doc/guide/objects) and materials (https://cyberbotics.com/doc/guide/appearances) and uses a GUI to modify the simulation. Webots use C, (https://cyberbotics.com/doc/guide/using-c) C++, (https://cyberbotics.com/doc/guide/using-cpp) Python, (https://cyberbotics.com/doc/guide/using-python) Java, (https://cyberbotics.com/doc/guide/using-java) MATLAB (https://cyberbotics.com/doc/guide/using-matlab) among others to program the robots.

Has Student Licence

5 - Software is open source

Blimp Physics Modeling Ability

5 - Yes, it has a blimp already modeled by the community

Ability to Modify Blimp Dimensions

4 - Yes, it can modify blimp dimensions

Ability to Modify Control Inputs

3 - yes, some ability to control inputs

Ability to Calculate Power Usage

2 - It seems to not have one

Ability to Measure Flight Path Deviation

2 - it seems not to have one but it can located the position of the center of mass of object

Ability to Visualize Simulation

5 - Yes, 3D simulation visualization

Has Common Scripting Language

5 - Yes, common lenguajes are C, C++, java, Python, Matlab

Gazebo
Gazebo is an open-source software simulator with a robust physics engine, high-quality graphics, and convenient programmatic and graphical interfaces. It has 4 physics engines including ODE, (http://opende.sourceforge.net/) Bullet, (http://bulletphysics.org/wordpress/) Simbody, (https://simtk.org/home/simbody/) and DART. (http://dartsim.github.io/) Custom plugins for robot, sensor, and environmental control could be developed, Also user inputs could be entered through a GUI or hardware controls. Ability to track simulation and sensor performance.

Has Student Licence

5 - Software is open source

Blimp Physics Modeling Ability

3 - No, it does not have a built-in blimp but it has an aerodynamics physics controller and it may have the ability to create one.

Ability to Modify Blimp Dimensions

3 - It has the ability to modify dimension but unsure about the blimp

Ability to Modify Control Inputs

3 - Yes it has the ability to control inputs

Ability to Calculate Power Usage

2 - No that I could read in the documentation

Ability to Measure Flight Path Deviation

2 - Yes, It has some kind of path deviation

Ability to Visualize Simulation

4 - yes, ability to visualize simulation but not totally sure with blimp

Has Common Scripting Language

1 - No, seems not to have one and run only in linux

EZPhysics
EZPhysics is a 3D simulation software and it uses Ogre 3D graphics library with ODE physics library. It builds characters by animating them using robotics control methods rather than playing pre-cooked motion sequences. EZPhysics makes it possible to create animated characters that really interact with the environment using closed-loop control techniques as do real robots. It is composed of different parts, an editor & simulator, a remote control protocol, and a C++ API.

Has Student Licence

5 - Software is open source

Blimp Physics Modeling Ability

1 - No, seems to not have one already built and difficult to build one

Ability to Modify Blimp Dimensions

2 - Yes, It has some ability to modify model

Ability to Modify Control Inputs

3 - Yes, it has the ability to control some inputs.

Ability to Calculate Power Usage

1 - No, it does not have one or at least documentation does not mention it.

Ability to Measure Flight Path Deviation

2 - Yes, it has a basic ability to follow the path

Ability to Visualize Simulation

3 - yes it has a not polished visualization but it has one

Has Common Scripting Language

5 - Yes, common languages C++, Python, and Matlab.

## 4.3 Primary Software: CopelliaSim

After careful consideration, including the use of the decision matrix in Table 1, it was decided that the best choice of software for the simulation of a blimp would be using CoppeliaSim. In addition to having a student license, CoppeliaSim allows easy importation of 3D models developed in other software, such as AutoCAD and Fusion
360. CoppeliaSim utilizes four different physics engines to simulate the interaction between objects.

Simulations in CoppeliaSim have local APIs in C and LUA and remote APIs in C, Java, Python, Matlab, and LUA. With model parameters defined in scripts, the software will be able to quickly make changes to model parameters without needing to recompile code. The software can be integrated with an existing ROS or BlueZero system for autonomous control of the simulation. It also has built-in modules for providing thrust and sensing, including proximity sensors and vision sensors.

It is notable that if student licensing was not a factor, Vortex Studio and WeBots would be good contenders for simulating blimps. Both focus on vehicle design which is suitable for blimp design and testing.

In short, CoppeliaSim will enable the model to be robust, but flexible, so that some analysis can be performed on the model’s performance in response to changes in different parameters like total mass or propeller placement.

## 4.4 Secondary Software: WeBots

Based on Table 1, it was decided that a second best choice of software for the simulation of a blimp would be Webost. In addition to having a student license, Webots allows easy importation of 3D models developed in other software, such as CAD files from Solidworks, Blender or from URDF. Webots core is based on the combination of a modern GUI (Qt), a physics engine (ODE fork) and an OpenGL 3.3 rendering engine (wren). It runs on Windows, Linux and macOS.

Simulations in Webots have local APIs in C and C++ and remote APIs in C, Java, Python, Matlab, or ROS. Model parameters are defined in nodes, but the controller is contained in a script and the software will be able to make changes to model parameters but the software needs to be compiled each time. It also has built-in modules for providing thrust and sensing, including proximity sensors and vision sensors.

In short, Webots will enable the model to be robust, but flexible, so that some analysis can be performed on the model’s performance in response to changes in different parameters like total mass or propeller placement.

## 5. Software Implementation

The main purpose of the software is to provide an environment for rapid development of a navigation AI for a physical blimp. To achieve this, the focus of the simulation will be to provide as many scenarios as possible for the AI to be tested within. The best way to provide a range of scenarios is to allow the user to easily modify the simulation from a single control board. Ideally this could be accomplished by a GUI, but may also be met with a text configuration file. The software can be used to evaluate several metrics including maneuverability, power usage, stability and minimum turning radius.

## 5.1 Maneuverability

Understanding the blimps maneuverability is important in order to evaluate a blimp AI’s effectiveness. A more effective blimp AI will have better maneuverability which will allow it to negotiate obstacles in its environment more effectively than a poor AI.

The maneuverability also depends greatly on the configuration of the motors, and the amount of thrust they are able to generate. Different motor configurations will provide different levels of maneuverability. Some configurations will allow for better control of altitude while others will allow the blimp to turn faster. Additionally, stronger motors will always have better maneuverability because they will be able to exert force at a faster rate.

The maneuverability of the blimp is measured by calculating the sum of the deviation from an intended path and dividing by the total distance of the path. For each simulation time step, the minimum distance from the intended path is calculated, and added together. This is the area of deviation. Once the path is completed, the area of deviation is divided by the number of time steps to calculate the blimp’s maneuverability.

## 5.2 Turning Method

Due to the blimp's inertia, the blimp will not always move in the direction the blimp is facing. This property is directly evident when the blimp makes a turn. If the blimp were to simply spin on the yaw axis it would not turn in the same way a car or airplane would. Instead, it would continue to move in the same direction, with an added motion in the direction the blimp spins. The effect of this is that the blimp will overshoot target waypoints.

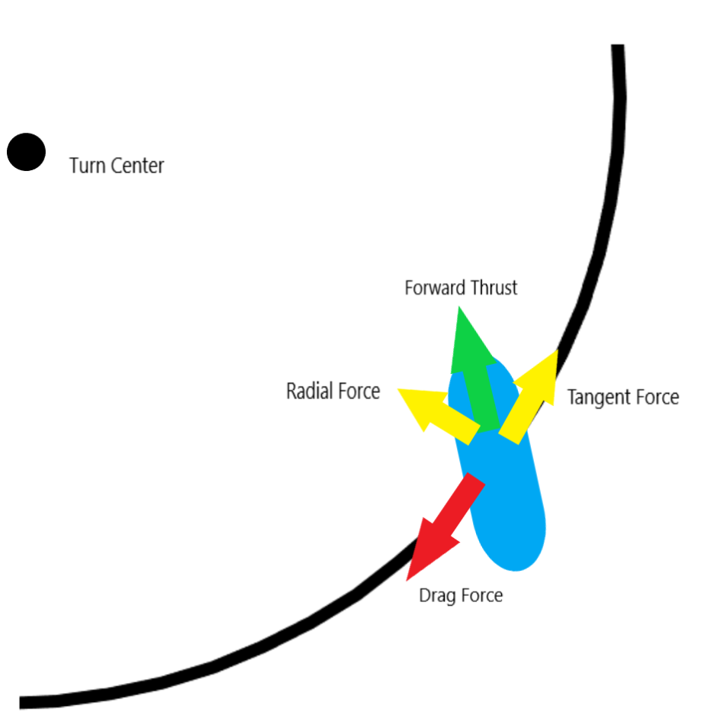
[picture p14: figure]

Figure 1: Turning Method

To overcome this restriction, a different method of turning must be implemented which takes into account the radial acceleration of the turn. Once a circular turn path is selected, the blimp must turn inward to face the center of the turn. If the blimp heading is directed at the center point throughout the turn, the blimp will coast through the turn, but will slow down due to air resistance. In order to maintain speed throughout the turn, the blimp heading must be adjusted toward the direction of motion such that the force tangent to the circular turn balances the drag from air resistance.

Once a desired turn is chosen, the maximum speed while navigating the turn can be calculated. The top speed of a turn depends on the maximum radial force that the blimp can exert. The required radial force for a given radius can be found with the following equation:

V | (1)
max

=

rF
r
m

Where m is the mass of the blimp, r is the radius of the turn, and Fr is the radial force exerted by the blimp. The max speed of the turn is best selected after determining the desired turn. It is important to account for the reduction of maximum thrust if the blimp employs a couple moment to control yaw articulation. Since the blimp will be rotating throughout the turn, one of the propellers must rotate at a slower speed in order to create yaw torque. This means the maximum forward thrust will be lower than the sum of the forward propellers.

Since the blimp will be able to move fastest when the turn is most shallow, the most shallow turn possible should be selected. Afterward, the top speed can be calculated for that course. If a slower speed is required, the blimp will be able to make the same turn at any speed below the calculated top speed.

If the blimp is attempting to reach a known waypoint within a short distance, the fastest way to reach the waypoint will be along a circle which intersects the waypoint and is tangent to the blimp's velocity, assuming this path does not interfere with the environment. The center of this circle can be easily found by finding the intersection of two lines. The first is a line through the blimp’s center of mass perpendicular to the velocity of the blimp, and the second is a line which bisects the blimp’s center of mass and the target waypoint. This path will allow the blimp to travel at the maximum speed along the shortest path without coming to a stop. When targeting waypoints at a greater distance, this method can be used to redirect the blimp in the direction of the waypoint before following a straight line to the target.

When non circular paths are desired, this method can still be used. At each point along a known non circular path, there will be a curvature and associated radial distance. By recalculating the desired circular path repeatedly and adjusting the center of the arc. The maximum curvature of such a path will depend not only on the maximum force that can be applied, but also on the maximum angular acceleration and velocity. In the case of the couple moment, the relevant ⍴feature of the blimp will be the distance between the horizontal props. In a design with a dedicated yaw control propeller, this will depend on the maximum force of that propeller.

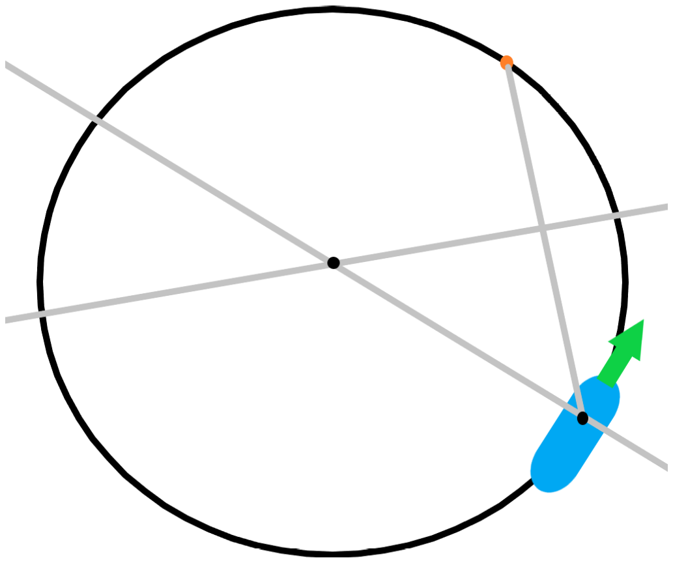
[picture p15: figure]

Figure 2: Finding the Turn Center

## 6. Component Analysis

## 6.1 Envelope

The envelope is the most difficult part of the blimp to obtain. Most premade balloons are not a sufficient size to avoid payload limitations. For this reason, most blimp applications will require a custom blimp envelope designed around the gondola and chosen components.

An important obstacle for the blimp is a standard doorway. In order to fit through a doorway, the maximum width for the blimp is roughly 0.5 m. For this reason, the best way to design the shape of the envelope is to start with an ellipsoid with b and c dimensions of 0.5m, and choose a dimension which will provide sufficient lift for the chosen components.

Unfortunately, very few companies are willing to make a blimp envelope at this scale. At a larger scale, premade blimp envelopes are available, in addition to several companies willing to fabricate custom envelopes. Likewise, if a smaller scale is achieved, a simple 18” mylar balloon can be used as the envelope. These simple party balloons have the advantage of being relatively cheap and easily accessible.

Because of its relative size, the envelope of the blimp will have the biggest impact on air resistance of the blimp as a whole. The air resistance of an ellipsoid can be calculated with the following equation:

D = | (2)

C
d

A⍴v

2

2

The coefficient of drag (Cd

) is dependent on the ratio of the major and minor diameters of the ellipsoid; the longer the ellipsoid, the lower the coefficient of drag. Since the dimensions of our blimp is dependent on the weight of the gondola, this value will change depending on which components are chosen for the blimp.

Considering a blimp a worst case Cd value of 0.13, we can calculate the worst case air resistance for our blimp’s envelope. For a blimp with a minor diameter of 0.5m and a top speed of 4 mph, the maximum air resistance will be 0.05 N. A more likely coefficient of drag for a blimp is 0.06, which will yield an air resistance of 0.02 N at 4 mph.

## 6.2 Chassis

The chassis gondola design is modeled for the criteria that the sponsors desire. These criteria were to allow different use cases to be developed over the course of the capstone project. As well, they could be verified through quantitative analysis and later on, simulations. Due to varying degrees of interest in the design of the chassis throughout the capstone project from the sponsor, only one design was built through to completion. This design was analyzed with SolidWorks to determine the potential aerodynamics of the model and interactions to the environment. Below are the categories of which the chassis design had considerations.

### 6.2.1 Overall Design

Figure 3 represents the gondola and blimp together as an illustration of how they would be seen in a physical model. The blimp envelope is shown to be 1.4 m while the gondola is ~22 x 10 x 8.5 cm, and weighs 80 grams without electrical components. The material that we chose to model for is PLA but have considered other materials like expanding foam. Within Figure 4, it shows the gondola design more precisely. It is also the design that was used to evaluate the aerodynamics.

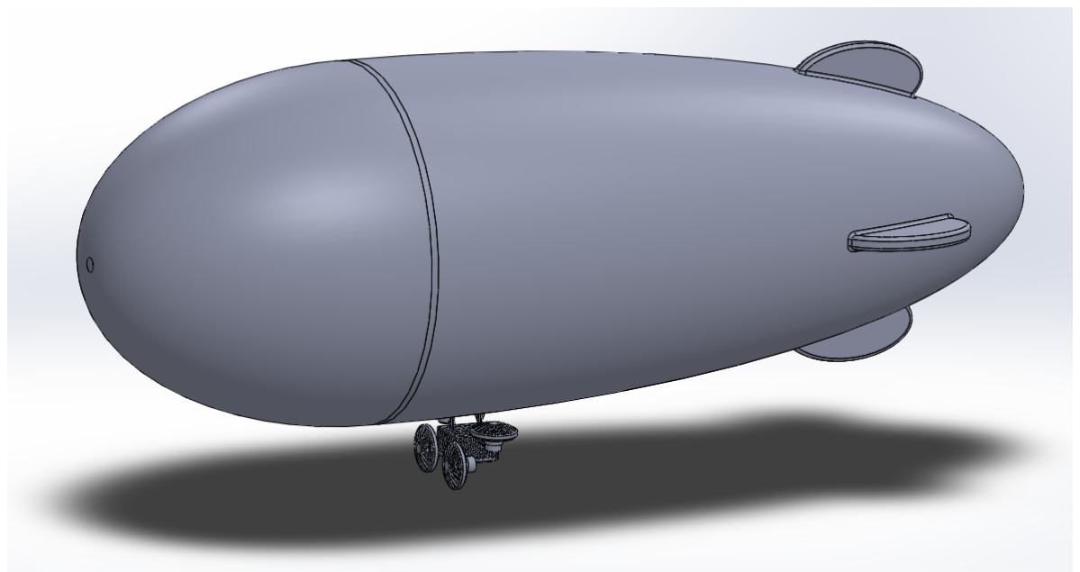
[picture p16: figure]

Figure 3: Overall Design with Blimp Envelope and Gondola


Figure 4: Model of the Gondola Design that is Expected to be 3D Printed

### 6.2.2 Modularity

The use case of modularity was important for the sponsor and user as they could change the position of the motors on the frame of the gondola. This could ensure that the frame would suit most cases in which parts changed or possibly the center of gravity would shift. Modulary was implemented through designing a hexagonal hole structure within the frame.

The hexagon shaped holes around the body are to allow protection of the electrical components within the housing. The holes also allow air flow through the housing to allow the electrical components to properly cool when the blimp is operating. The shape of the holes are to offer a modular design

### 6.2.3 Aerodynamics:

The gondola design was evaluated within the Flow Simulation in Solidworks to determine the change in pressure and velocity while interacting with the CAD model. The analysis of the design is elementary and was to show a representation of which parts of the design could impact the aerodynamics the most. Though, in the applications of this blimp, aerodynamics shouldn’t affect the movement of the whole system. This is evident with the results found in figures one and two as they show the pressure and velocity drop as it passes across the design. Figures three and four show how the flow simulations were constructed to gather the data and calculations.

The results show that the model of the gondola causes a slight drop in pressure and a greater drop in velocity. It would be recommended that more analysis be done to have a

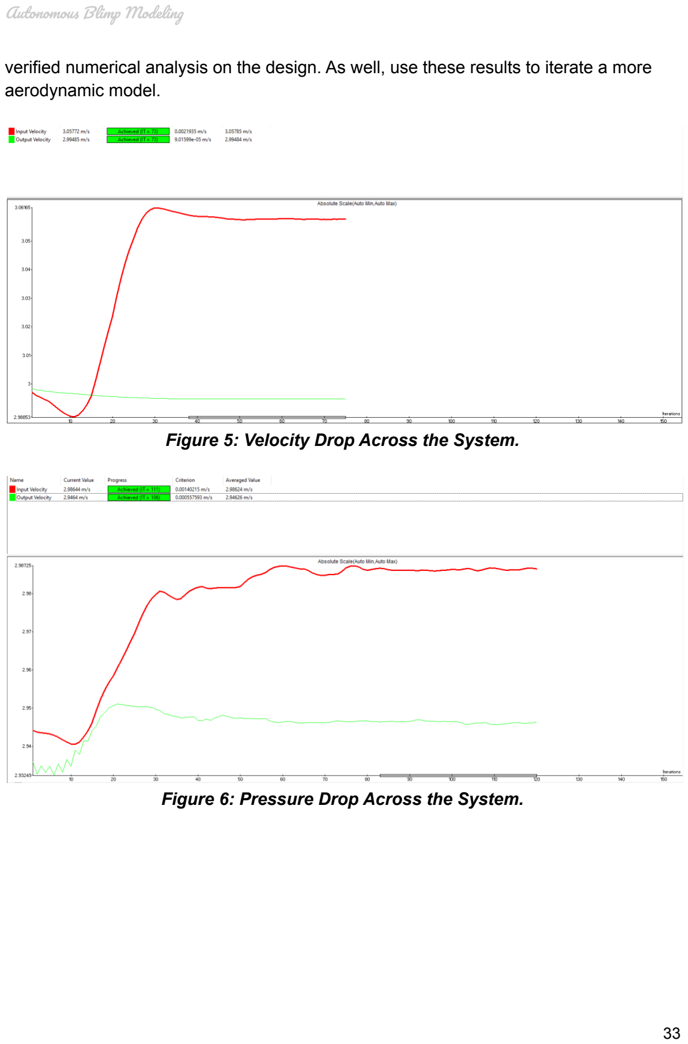
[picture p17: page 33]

verified numerical analysis on the design. As well, use these results to iterate a more aerodynamic model.

Figure 5: Velocity Drop Across the System.

Figure 6: Pressure Drop Across the System.

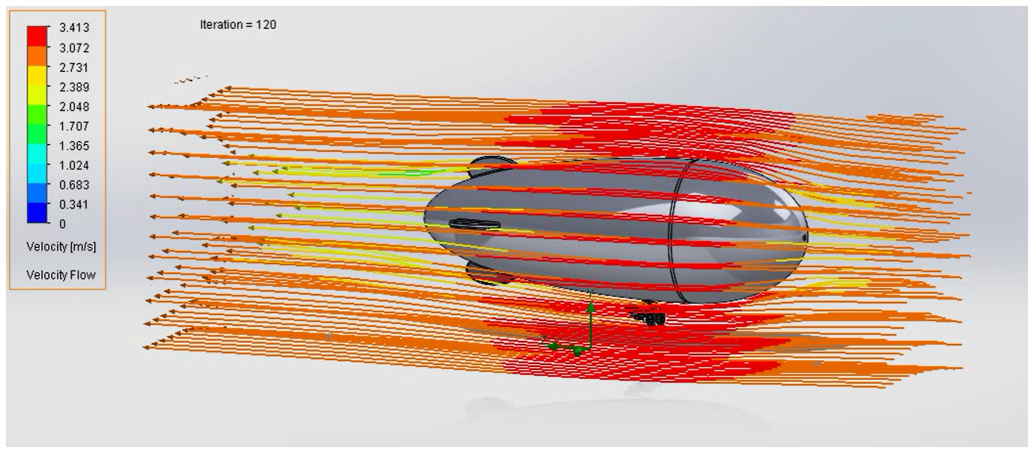
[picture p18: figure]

Figure 7: Flow of Air Interacting with the Complete Blimp Design.

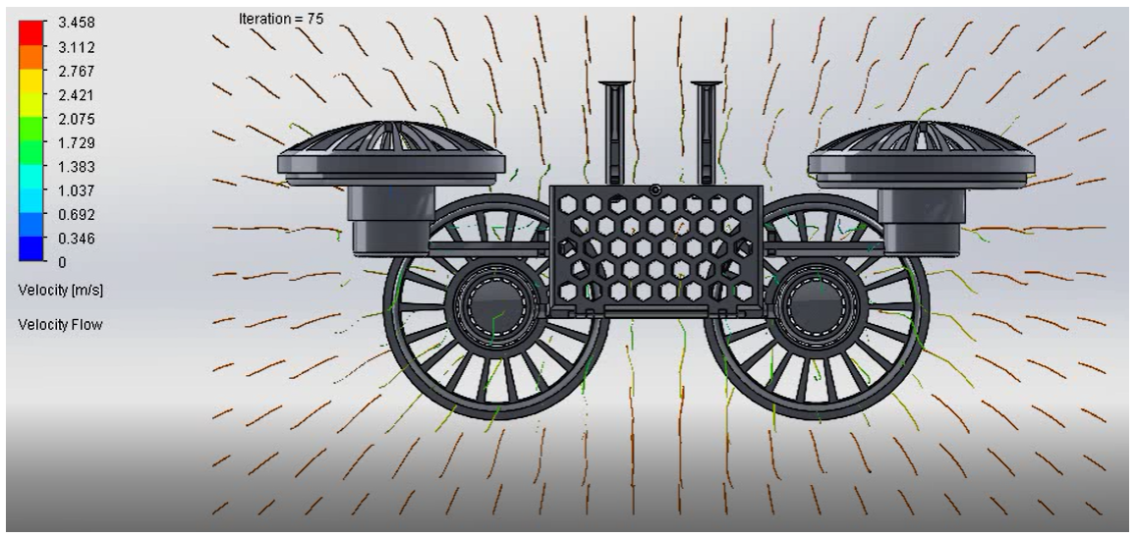
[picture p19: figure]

Figure 8: Movement of Air Passing through the Gondola

### 6.2.4 Mass

As the blimp is a lighter than air vehicle, the mass plays an important role in determining the amount of payload allowed. This was a design consideration when looking at the design of a structural and functional chassis. For this, it was considered how the parts would be manufactured on a 3D printer. To reduce weight, it was discussed changing the infill or the material used for the gondola. As well, looking at the amount of holes in the design, which requires a 3D printer to outline with a thicker wall.

### 6.2.5 Future Design Considerations

These future design considerations are to assist in the future possibility of bringing this capstone project into a physical model.

Due to the time constraints with the project, it would be advantageous to look into other considerations of the designed chassis. One design criteria should be looked into the implemented velcro design life. How many cycles could a velcro system be sustained before the velcro no longer performs at an acceptable level. Another criteria that would be significant to consider is overall strength of the gondola parts. It would be valuable to investigate the bending strength of the prototyped parts and material. Finally, a more in depth analysis of the aerodynamics of how the gondola affects the movement of the blimp could be significant.

## 6.3 Motors

The type of motor to be used depends heavily on the size of the blimp being made. For a very small blimp the obvious choice is a brushed DC motor. These motors are electrically simple and do not require separate ICs to drive them. Since the motors are not intended to be spinning for the entire duration of the run time, the life of the motors will also not be a limitation. Brushed DC motors can be made very small for the smallest blimps, but also scale up to medium sized indoor blimps. These motors can range from $2 to $100, although motors which cost more than $20 would likely be better replaced with brushless AC motors.

Brushless DC motors are not a good choice for blimp propulsion. They are usually designed to have high torque but relatively low power output. They are also very heavy for their power output as well.

At larger scales, a brushless AC motor is likely a better choice. These motors have a high power output, but are relatively heavy compared to brushed DC motors. The larger scale means the AC motor driver will not be a meaningful weight addition to the blimp. Additionally, non neutral buoyancy will need to be counteracted with a vertically oriented motor, which will need to be running any time the blimp isn’t tethered. Brushless AC motors are ideal for this situation because they do not have brushes which can wear out over time. These motors cost $10 and up depending on the power output needed.

At very large scales an internal combustion engine may be the best choice. Electric motors are limited by the batteries that power them because batteries are very heavy for the amount of power they can hold. Compared to batteries, gasoline has a very high energy density and will be able to provide propulsion with a lower impact on payload weight.

Motor power depends heavily on the desired characteristics of the blimp. However, a small blimp weighing around 2 lbs will be able to maneuver at a reasonable speed with motors rated between 1 and 5 watts. A larger blimp of 10 lbs will require more power, between 10 and 15 watts. In general, for an acceleration of 1 m/s^2 a blimp should have a motor which produces 1W for every Kg the blimp weighs.

## 5.4 Props

Motor thrust will depend on the dynamics of the propeller. Fortunately, in most cases the blimp will produce more than enough power to move the blimp. For this reason, a propeller should be chosen to maximize the motor’s efficiency. Each motor will have varying efficiency throughout its rpm range. The propeller should be chosen such that the desired maximum force from the motor will occur near the motor's peak efficiency. This will reduce the power being used by the blimp, and extend the blimp’s life between charges.

If blimp maneuverability is desired above efficiency, the propeller should instead be chosen which maximizes force at full power. This will be less efficient, but will allow for greater blimp maneuverability and top speed.

## 6.5 Batteries

Since the weight of the blimp is such an important metric, it is important to pick a battery which has a very high power density. One good choice to meet this requirement is the LiPo battery. These batteries have good power density and come in a wide range of sizes and power ratings. However, it is important that these types of batteries be charged with a LiPo specific charger to avoid starting a fire.

NiMh batteries are another good choice. While they do not offer the same power density as LiPo batteries, they are much more stable and do not require a special charger. They are also cheaper than LiPo batteries for the same power volume. NiMh batteries take longer to charge as well but this will not be important if the blimp has periods of down time.

## 7. Conclusion

Through the use of simulation software this project intended to learn about the dynamics of blimp movement in order to choose effective propeller configuration, important components, and design a gondola chassis.The plan was to simultaneously develop a simulation program and a CAD model. During this process both scenarios would be optimized.

The main purpose of the software was to provide an environment for rapid development of a navigation AI for a physical blimp. The software was used to evaluate some metrics including maneuverability, power usage, stability and minimum turning radius. The use of simulation software was important to our understanding of blimps, like their physics and how to apply forces and torque to the motors. One of the challenges was to adapt a turning method to and apply it to the blimp, we had some success implementing it.

The team constructed a 3D computer aided design using SolidWorks. The design integrated several different design criteria based on the desires from Galois Inc. The model specifically took into account modularity, airflow over electrical components, protection, and manufacturability. The development of the CAD model investigated the performance of aerodynamics and the influence it had on velocity and pressure. The design's function is to be used concurrently with the simulations to repetitively design an optimal design.

The team’s recommendation is to use both of the simulations (CopelliaSim and Webots) to develop a more robust analytical tool for future use. The function of using both simulations is to construct different environmental constraints and situations and have the software eventually be refined into an AI system. Another recommendation is for the team successor to use SolidWorks to construct further analysis on the gondola and blimp design. The reasoning is because the original construction of the gondola was designed in SolidWorks, so making changes would be uncomplicated. SolidWorks also has a set of rigorous simulation functions that can be used to evaluate the aerodynamics, finite element analysis, and mass properties of the whole system.

The work that has been done through this capstone project is expected to be developed further through Galois. The deliverables allow an introduction and a path for future investigators to implement a physical model. With the usage of a simulation that has been completed and a gondola design, it is expected that the future team will work iteratively through different blimp designs to find an optimal solution for Galois and the DARPA competition.

## 8. Works Cited

1.
P. Burgers, “A thrust equation treats propellers and rotors as aerodynamic cycles and calculates their thrust without resorting to the blade element method,” Scholarly Commons, 2019. [Online]. Available: https://commons.erau.edu/cgi/viewcontent.cgi?article=1427&context=ijaaa. [Accessed: 08-Jun-2021].
2.
“Ellipsoid Surface Drag, Drag Coefficient Equation and Calculator,” Engineers Edge. [Online]. Available: https://www.engineersedge.com/fluid_flow/ellipsoid_surface_drag_14047.htm. [Accessed: 08-Jun-2021].

## 9. Table of Figures

Figure 1: Turning Method | 28
Credit: Jacob Thomas
Figure 2: Finding the Turn Center | 29
Credit: Jacob Thomas
Figure 3: Overall Design with Blimp Envelope and Gondola | 31
Credit Dylan Filkins
Figure 4: Model of the Gondola Design that is Expected to be 3D Printed | 32
Credit: Dylan Filkins
Figure 5:Velocity Drop Across the System | 33
Credit: Dylan Filkins
Figure 6:Pressure Drop across the System | 33
Credit: Dylan Filkins
Figure 7: Flow of Air Interacting with the Complete Blimp Design | 32
Credit: Dylan Filkins
Figure 8:Movement of Air Passing Through the Gondola | 32
Credit: Dylan Filkins

## 10. Annotated Bibliography

Citation:

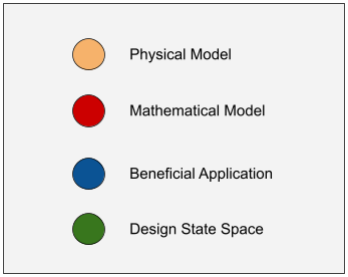
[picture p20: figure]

Tao, Qiuyang & Tan, Tun & Cha, Jaeseok & Yuan, Ye & Zhang, Fumin. (2020). Modeling and Control of Swing Oscillation of Underactuated Indoor Miniature Autonomous Blimps. Unmanned Systems. 09. 10.1142/S2301385021500060. https://www.researchgate.net/publication/340883576_Modeling_and_Control_of_Swing_Oscillation_of_Underactuated_Indoor_Miniature_Autonomous_Blimps (https://www.researchgate.net/publication/340883576_Modeling_and_Control_of_Swing_Oscillation_of_Underactuated_Indoor_Miniature_Autonomous_Blimps)

Summary:
This report goes into the basic setup of a circular autonomous blimp (developed at Georgia Tech). It describes their dynamic model calculations for pitching. The paper goes into the background of linearization of their equations to come up with benchmarks of their data that they collected. As well, the paper explores the oscillation motion with graphical representation of the motion captured. The paper also goes into the calculations of buoyancy, lift, and the moment of inertia. All calculations were done in Matlab.

System Specs:
Electronics Mass: 107.24 grams
PCB: Arduino Uno & XBee attachment Flight Endurance: 2 hours
Helium Mylar Film: ~8 grams Program: Matlab

Citation:
Nitta, Yoshihiro et al. “The Visual Inspection Methodology for Ceiling Utilizing the Blimp.” Procedia Engineering. Vol. 188. Elsevier Ltd, 2017. 256–262. Procedia Engineering. Web.
https://www-sciencedirect-com.proxy.lib.pdx.edu/science/article/pii/S187770581732034 9 (https://www-sciencedirect-com.proxy.lib.pdx.edu/science/article/pii/S1877705817320349)

Summary:
This report describes the advantages blimps could offer over drones for inspecting buildings for structural damage. The report offers minimal design considerations but goes into detail on which electronics are used.

The electronics used are a microcontroller that is an open-source 8-bit RISC-based platform, an Arduino Micro, two motors, and two servos. The Arduino Micro controls two servo motors with 2ch pulse-width modulation signals and two motors with two digital signals. With one of the servos in control of the wifi-enabled camera and the other to move the vertical motor arm. The camera used is a 1/9 inch CMOS sensor with 300,000 pixels and 802.11 b/g Wi-Fi interface. The two motors attached to the gondola control the horizontal and vertical motion of the propellers respectively. The system is powered by three batteries. Two 3.7V Li-Po batteries power the motors and servos and the last one is a rechargeable battery to power the wifi camera.

System Specs:
Total Mass: 300 grams
PCB: Arduino Wifi Micro
Flight Endurance: 1 hour
Helium Aluminum Film
Cost: $350

Citation:
Jinjun Rao, et al. “A Flight Control and Navigation System of a Small Size Unmanned Airship.” IEEE International Conference Mechatronics and Automation, 2005, July 2005, doi:10.1109/icma.2005.1626776.
https://ieeexplore.ieee.org/document/1626776

Summary:
This report described in detail the H/ W and S/ W and flight controllers for a blimp used in a designated simulation space. The report goes into extensive detail about what hardware and software they used. It also goes into detail about the controllers used in their system with Fuzzy Controller, elevator controller, and a heading controller. The authors also describe the design space of the blimp and use Matlab to calculate the necessary parameters. The paper also describes how they simulated the blimp in Matlab to get a better understanding graphically and spatially for their design.

System Specs:
Helium Volume: 50 m^3
Payload: 15 kg
Max. Velocity: 60 km/h
Program: Matlab

Citation:
Zufferey, Jean Christophe et al. “Flying over the Reality Gap: From Simulated to Real Indoor Airships.” Autonomous Robots 21.3 (2006): 243–254. Autonomous Robots. Web. https://doi-org.proxy.lib.pdx.edu/10.1007/s10514-006-9718-8

Summary:
The report goes into extensive detail about mechanics theory. It goes through the detailed proof of the dynamic modeling of the blimp so that it could be employed later in a simulation. The Newton-Euler equation is used to link the acceleration to the moments and forces applied to the blimp. The simulation model is done through Webots and a targeted path coordination was optimized through it. The team also looked at image recognition with the usage of simulations.

The electronics and hardware are detailed in the following. Three thrusters (8 mm DC motors, gear, and propellers), a forward-looking 1D camera (Taos inc. TSL3301) with 50 active pixels covering a horizontal field of view of 70◦, an anemometer, a vertical distance sensor (SharpTM GP2Y0A02YK), a MEMS piezoelectric rate gyro (AnalogDevicesTM ADXRS300) measuring yaw rotation, and an electronic board featuring an 8-bit microcontroller running at 20 MHz (MicrochipTM PIC18F452) together with a Bluetooth module (MitsumiTM WML-C10-AHR) for bidirectional wireless communication with a ground station. On-board energy is provided by a 1200mAh Lithium-polymer battery, which is sufficient for 2–3 hours of autonomy. Further details on the microcontroller board, wireless link, and camera.

System Specs:
The envelope measures: 110 × 60 × 60 cm
Lift Capacity: 200g

Parts: 3 DC rotors, ID Camera, vertical distance sensor, gyro, 1200mh lithium battery, and 8bit microcontroller running at 20 Mhz

Citation:
Palossi, Daniele et al. “Self-Sustainability in Nano Unmanned Aerial Vehicles: A Blimp Case Study.” ACM International Conference on Computing Frontiers 2017, CF 2017. Association for Computing Machinery, Inc, 2017. 79–88. ACM International Conference on Computing Frontiers 2017, CF 2017. Web. https://dl-acm-org.proxy.lib.pdx.edu/doi/abs/10.1145/3075564.3075580

Summary:
The report goes into detail about how to achieve low power consumption using the duty cycle, as the blimp rotor was turned on and off. It does not go into detail about hardware but has a list of materials. Also, they used a solar cell attached to the blimp to extend the flight time, and they argue that it can stay several hours flying.

Basic mathematical equations are employed as a way to describe a blimp, but not of significant importance towards our use case.

The journal does describe the power usage management with software and NRF51 firmware to optimize the system as a whole.

System Specs:
The blimp measures: 0.4m3
Weight: 55g
Parts: solar panel, MCU, battery, harvester, and rotor.

Citation:
Zheng, Zewei, Huo, Wei, & Wu, Zhe. (2013). Autonomous airship path following control: Theory and experiments. Control Engineering Practice, 21(6), 769–788. https://doi.org/10.1016/j.conengprac.2013.02.002

Summary:
The report looks into the mathematical model and simulation framework for the movement of a blimp 3D space. This is done through its simulation data and practical testing afterward. Goes into significant detail about how the mathematical model is achieved. The students used the guidance-based path following (GBPF) principle and trajectory linearization control (TLC) theory to explain their dynamic modeling.

As well goes into controller diagrams and explanations of it.

Specs:
Length: 13.2 m
Diameter: 3.38 m
Volume: 80m^3

Citation:
Ko, Jonathan et al. “Gaussian Processes and Reinforcement Learning for Identification and Control of an Autonomous Blimp.” Proceedings - IEEE International Conference on Robotics and Automation. N.p., 2007. 742–747. Proceedings - IEEE International Conference on Robotics and Automation. Web. https://ieeexplore-ieee-org.proxy.lib.pdx.edu/document/4209179

Summary:
The academic goes into the basic knowledge of the below topics and summarizes other academic articles. The article does a good job looking at the topics in a holistic and simplistic manner. The topics can be easily understood due to the summarization of other academic articles and the high arching overview of them. A benefit of this article is that it has links and references to all the articles that it reviews. The article also goes into a simplistic overview of control systems and autonomous control systems.

Topics:
-Motion Control
-Navigation Control
-Control Methods (PID)
-Controlling Algorithms
-Backstepping Controls
-Model-Predictive Control
-Autonomous Control Systems

Citation:
Wang, Yue et al. “Altitude Control for an Indoor Blimp Robot.” IFAC-PapersOnLine 50.1 (2017): 15990–15995. IFAC-PapersOnLine. Web. https://www-sciencedirect-com.proxy.lib.pdx.edu/science/article/pii/S240589631732536 3 (https://www-sciencedirect-com.proxy.lib.pdx.edu/science/article/pii/S2405896317325363)

Summary:

This report goes into detail briefly the parameters for the altitude control model, create simulation and apply it to the physical blimp. The end goal is for an autonomous blimp with a feedback loop of position of the environment to navigate.

System Specs:
Total Payload: 250 grams
PCB: Arduino FIO
Flight Endurance: 1 hour
Envelope: nylon 132cm length, 94cm diameter Sensors: ultrasonic sensor, IMU, Camera, Xbee unit, 3 mini rotors.
Simulation: matlab Simulink

Citation:
Alsayed, Ahmad, and Eric Lanteigne. “Experimental Pitch Control of an Unmanned Airship with Sliding Ballast.” 2017 International Conference on Unmanned Aircraft Systems (ICUAS), 2017, doi:10.1109/icuas.2017.7991326. http://hdl.handle.net/10393/36594

Summary:
The report describes the mathematical model, simulation and experimental results of a blimp with a gondola with and without wind disturbances. Author wanted to develop a close-loop control for a blimp using altitude and pitch using the gondola on a rail that can move as one of the inputs. Blimp was simulated in Matlab/simulink and control used a matlab GUI. simulation results were compared to experimental data/tests.

Topics:
-Motion Control
-Navigation Control
-Control Methods (PID)
-Controlling Algorithms (matlab GUI) -Autonomous Control Systems

System Specs:
Total Payload: 350 grams
PCB: Nano Wii board
Flight Endurance: 1 hour
Envelope: 2 Mil polyester
polyurethane lm with 90 Shore A hardness length is 1.83 m, volume 0.39 m3, and diameter is 0.6 m. Sensors: bluetooth modules, IMU, 2 mini rotors. Simulation and control: matlab Simulink / GUI
Battery: 2 cell 7.4V

Citation:
Boardman, Beth, and Linh Bui. “AA 449 Final Milestone Report Blimp Project.” (2010): 1–55. Print.
https://www.washington.edu/search/?q=Final+Milestone+Report+Blimp+Project

Summary:
The report describes the mathematical model, simulation and experimental results of a blimp with a gondola. Author wanted to develop and control the blimp using 5 propellers. Blimp was simulated in Matlab/simulink and control used a matlab GUI. simulation results were compared to experimental data/tests

Topics:
-Motion Control
-Navigation Control
-Control Methods (PID)
-Controlling Algorithms (matlab GUI) -Autonomous Control Systems

System Specs:
Motor: bidirectional propellers Total Payload: 350 grams
PCB: Arduino Duemilanove
Envelope: 4 foot diameter

## 10. Simulation Softwares

Physics Abstraction Layer
The Physics Abstraction Layer (PAL) provides a unified interface to a number of different physics engines. This enables the use of multiple physics engines within one application. It is not just a simple physics wrapper, but provides an extensible plug-in architecture for the physics system, as well as extended functionality for common simulation components.

Website: http://www.adrianboeing.com/pal/index.html

Reference Manual: http://www.adrianboeing.com/pal/documentation.html User Guide: http://www.adrianboeing.com/pal/benchmark.html

Simulink
Simulink®
is a block diagram environment for multi domain simulation and Model-Based Design. It supports system-level design, simulation, automatic code generation, and continuous test and verification of embedded systems. Simulink provides a graphical editor, customizable block libraries, and solvers for modeling and simulating dynamic systems. It is integrated with MATLAB®
, enabling you to incorporate MATLAB algorithms into models and export simulation results to MATLAB for further analysis.

Website: https://www.mathworks.com/help/simulink/
Reference Manual: ttps://www.mathworks.com/help/simulink/simulink-environment.html User Guide: https://www.mathworks.com/help/simulink/getting-started-with-simulink.html

CoppeliaSim
The robot simulator CoppeliaSim, with integrated development environment, is based on a distributed control architecture: each object/model can be individually controlled via an embedded script, a plugin, a ROS or BlueZero node, a remote API client, or a custom solution. This makes CoppeliaSim very versatile and ideal for multi-robot applications. Controllers can be written in C/C++, Python, Java, Lua, Matlab or Octave

Website: https://www.coppeliarobotics.com/
Reference Manual: https://www.coppeliarobotics.com/features
User Guide: https://www.coppeliarobotics.com/helpFiles/index.html

Vortex Studio
Vortex Studio is CM Labs’ advanced suite of real-time simulation and visualization software, a high-fidelity platform for fast-paced, user-centric mechanical prototyping, streamlined product design and deployment of immersive virtual experiences for human-in-the-loop testing, immersive training, and enhanced marketing experiences.

Website: https://www.cm-labs.com/vortex-studio/
Reference Manual:
User Guide:

RoboLogix
RoboLogix is a state-of-the-art robotics simulation software package that is designed to emulate real-world robotics applications. With RoboLogix, you teach, test, run, and debug programs that you have written yourself using a five-axis industrial robot in a wide range of practical applications. These applications include pick-and-place, palletizing, welding, painting and allow for customized environments so that you can design your own robotics application. With RoboLogix, the user can run the simulator to test and visually examine the execution of robot programs and control algorithms.

Website: https://robologix.com/
Reference Manual: https://www.robologix.com/robologix_overview.php
User Guide: https://www.robologix.com/programming_robologix.php

SimulationX
With SimulationX, you have a single platform for modeling, simulating, and analyzing technical systems, including mechanics, hydraulics, pneumatics, electronics, and controls, as well as thermal, magnetic, and other physical behavior. Comprehensive component libraries with application-oriented model elements ensure you have the right tools available for your task.

Website: https://www.esi-group.com/products/system-simulation
Reference Manual:
User Guide:

Webots
Webots is an open-source and multi-platform desktop application used to simulate robots. It provides a complete development environment to model, program, and simulate robots.
It has been designed for professional use, and it is widely used in industry, education, and research. Cyberbotics Ltd. has maintained Webots as its main product continuously since 1998.

Website: https://www.cyberbotics.com/#features
Reference Manual: https://www.cyberbotics.com/doc/reference/thanks
User guide: https://www.cyberbotics.com/doc/guide/index

Gazebo
Gazebo offers the ability to accurately and efficiently simulate populations of robots in complex indoor and outdoor environments. At your fingertips is a robust physics engine, high-quality graphics, and convenient programmatic and graphical interfaces. Best of all, Gazebo is free with a vibrant community.

Website: http://gazebosim.org/
Reference Manual(API):

http://osrf-distributions.s3.amazonaws.com/gazebo/api/11.0.0/index.html
User guide: http://gazebosim.org/tutorials

EZPhysics
EZPhysics integrates Ogre 3D graphics library with ODE physics library. It aims to breathe life into 3D game characters by animating them using robotics control methods rather than playing pre-cooked motion sequences.

Website: http://ezphysics.org/joomla/
User guide: http://ezphysics.org/joomla/index.php?option=com_jfusion&Itemid=83

## Revisions

Revision 2.0: 03/31/2021: Initial document.
Revision 2.1: 04/02/2021: Added sections, Formatting.
Revision 2.2: 04/04/2021: Added info and software research, Formatting. Revision 2.3: 04/07/2021: Added info to Ch1, Ch3, Ch4.
Revision 2.4: 04/08/2021: Added info to Ch5, Formatting.
Revision 2.5: 04/16/2021: Added items table of Contents, Added info various. Revision 2.6: 04/23/2021: Added items Table of contents, Added info to Ch4. Revision 2.7: 04/30/2021: Added Info to Ch4.
Revision 2.8: 05/07/2021: Added Ch5.
Revision 2.9: 05/14/2021: Added info to Ch5.
Revision 3.0: 02/21/2021: Added info to Ch4. Revision 3.1: 05/28/2021: Added info to Ch3, CH5. Revision 3.2: 06/08/2021: Formatting.

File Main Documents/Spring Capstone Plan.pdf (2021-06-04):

| Day | Date | Recurring Tasks | Team Goals
1 | S | 3/28/21 M 3/29/21 3/30/21 W 3/31/21 Th 4/1/21 4/2/21 4/3/21 | 1000 Team Meeting T 1000 Sponser Meeting F Progress Report S
2 | S | 4/10/21 | | Revise Blimp Design Document | Read AA 449 Final Milestone Report Blimp Project Edit the Introduction section and continue to add to it, Look at annotated Bib. due to Dr. Faust comments Write Blimp Performance Characteristics

Individual Deliverables RED-COMPLETE

Ben | Victor | Nick | Jacob | Dylan | Zeming
S | 4/4/21 M | 4/5/21 | 1000 Team Meeting T | 4/6/21 W | 4/7/21 | Finish Blimp Design Document and send to sponsor | Assist with writting Metrics | Write Software chapter introduction, Review Design Space chapter Draft outline for Introduction section for the FOCUS document | Select some of the originals you need in your design Th | 4/8/21 | 1000 Sponser Meeting | Discuss Blimp Design document with Sponsor | Review Metrics section with Jacob and format information into new doc Write Software chapter introduction, Review Design Space chapter | Write Chapter 3: Metrics | Finish comments for Dr.Faust F | 4/9/21 | Progress Report | Revise Blimp Design Document, Review Metrics section from previous doc, Begin Project Wiki Decide Best software, Review chapter details | Decide Best Software | Decide Best Software | Decide Best Software | Review the Design Space section of the document, Introduction Rough Draft Review the Design Space section of the document, Introduction Rough Draft

3

S | 4/11/21 | Revise Blimp Design Document | Read AA 449 Final Milestone Report Blimp Project | Design and update project wiki | Design a dynamic equations model document (Engineering Analysis), Come up with presentation matter for Annotated Bib. Write Chapter 3: Metrics M | 4/12/21 | 0900 Team Meeting | Revise Blimp Design Document to final draft and send to sponsor | Impliment suggestions/corrections from Mark | Design and update project wiki | update capstone plan | Finish a dynamic equation documentation for the simulation team and for report Write Chapter 3: Metrics T | 4/13/21 | Impliment suggestions/corrections from Mark | Design and update project wiki | Refine the Introduction section and start to implement a "storyline" to blimps looking at Dr.Per contri. Learn mathematics about airship design W | 4/14/21 | Research methods of testing blimp for Ch 3 | Design and update project wiki | achieve stationary blimp simulation | Write explanations for metrics | Assist in the writing in metrics, performance, design space, start reading Dr. P +65 paper. Read different reports to check for required originals Th | 4/15/21 | 1000 Team Meeting | Create a rough test for simulation for Ch 3 | Design and update project wiki | Add control surfaces | Write explanations for metrics | Start to create a journal presentation to present to the other team members, as not all have read the papers Perfect the information that needs to be perfected in document F | 4/16/21 | Progress Report | Review Ch 4 metrics table with Team | Design and update project wiki | control propellers with exteral code | Write explanations for metrics | Finish +65 paper from Dr. Per. | Read the completed report S | 4/17/21 | Read into simulation/ get a debrief from the simulation team on simulations

4

S | 4/18/21 | Create comprehensive dynamic modeling equations of blimp M | 4/19/21 | 0900 Team Meeting | Achieve basic blimp simulation | Finalize testing | Begin stationary blimp using webots | Achieve Controled flight with code | Write detailed summary of chosen software and secondary software Start second +80 paper from Dr. Per T | 4/20/21 | Assist with prototype gondola design | add control surfaces | Refine Controled flight | Write detailed summary of chosen software and secondary software Start Prototype design (Gondola) | Assist Prototype Design: Thrusters(The drive module of the motor W | 4/21/21 | Assist Prototype Design: Thrusters | prepare simulation for sponsor presentation | prepare simulation for sponsor presentation | Write detailed summary of chosen software and secondary software Prototype Design: Thrusters | Assist Prototype Design: Thrusters(The drive module of the motor Th | 4/22/21 | 1000 Sponser Meeting | Present basic blimp simulation to sponsor | Assist Prototype Design: Thrusters | Present basic simulation to sponsor | Present basic simulation to sponsor | Present basic simulation to sponsor | Prototype Design: Thrusters | Prototype Design: Thrusters F | 4/23/21 | Progress Report | Assist Prototype Design: Cage | Review lessons from simulation creation and sponsor input Review lessons from simulation creation and sponsor input Review lessons from simulation creation and sponsor input Prototype Design: Cage | Prototype Design: Cage S | 4/24/21 | Finish second +80 Paper from Dr. P

5

S | 4/25/21 | Prototype Design: Cage | Prototype Design: Cage M | 4/26/21 | 0900 Team Meeting | Prototype Design: Cage door | integrate metrics measurement | integrate metrics measurement | Begin chapter on Blimp components | Prototype Design: Cage door | Prototype Design: Cage door T | 4/27/21 | Prototype Design: Cage door | integrate metrics measurement | integrate metrics measurement | Begin chapter on Blimp components | Prototype Design: Cage door | Prototype Design: Cage door W | 4/28/21 | Prototype Design: Envelope Attachment | integrate metrics measurement | integrate metrics measurement | envelope | Prototype Design: Envelope Attachment | Prototype Design: Envelope Attachment Th | 4/29/21 | 1000 Sponser Meeting | Refine blimp simulation, add movement and plan for sponsor to add autonomy | Prototype Design: Envelope Attachment | Communicate metrics measurement with sponsor and make changes based on input Communicate metrics measurement with sponsor and make changes based on input envelope | Prototype Design: Envelope Attachment | Prototype Design: Envelope Attachment F | 4/30/21 | Progress Report | Design iteration: With Dylan | integrate metrics measurement | integrate metrics measurement | Design iteration: With Ben S | 5/1/21 | Design iteration: With Dylan | Design iteration: With Ben

6

S | 5/2/21 | Design iteration: With Dylan | Design iteration: With Ben M | 5/3/21 | 0900 Team Meeting | Design Choice (Grams per design calculation) | set up flight path simulation demonstration | set up flight path simulation demonstration | Design Choice (Grams per design calculation)Design Choice (Grams per design calculation) T | 5/4/21 | Design Choise (Best component ranking) | set up flight path simulation demonstration | set up flight path simulation demonstration | Design Choise (Best component ranking) | Design Choise (Best component ranking) W | 5/5/21 | Begin working on Capstone presentation | Prepare for Presentation | polish final blimp simulation for sponsor | polish final blimp simulation for sponsor | create governing equation | Prepare for Presentation | Prepare for Presentation Th | 5/6/21 | 1000 Sponser Meeting | Present final simulation to sponsor (sponsor handoff?) | Present Physical Blimp Airframe Design | Present Blimp Simulation | Present Blimp Simulation | create governing equation | Present Physical Blimp Airframe Design | Present Physical Blimp Airframe Design F | 5/7/21 | Progress Report | Send Jacob Prototype for 3D printing | Reflect on Project Deliverables in silence | Reflect on Project Deliverables in silence | create governing equation | Reflect on Project Deliverables in silence | Reflect on Project Deliverables in silence S | 5/8/21 | Investigate Mass Moment of Inertia

7

S | 5/9/21 | Redesign blimp for the printablilty M | 5/10/21 | Jacob responce/ critique on final prototype | fix/integrate features to blimp after sponsor feedabck | design headding controller | Give Masss Moment of Inertia data | Build a simulation model of an airship T | 5/11/21 | 0900 Team Meeting | Corrections on prototype design | fix/integrate features to blimp after sponsor feedabck | design headding controller | Integrate Ben's design of propeller shroud | Build a simulation model of an airship W | 5/12/21 | Corrections on prototype design | fix/integrate features to blimp after sponsor feedabck | turning radius measurement | CRA for Solidworks files | Modify the data for the physical model Th | 5/13/21 | 1000 Sponser Meeting | Send Jacob Prototype for 3D printing | present to Sponsor | turning radius measurement | Present Physical Blimp Airframe Design | Modify the data for the physical model F | 5/14/21 | Progress Report | Any further corrections after 3D printing | Reflect on Project Deliverables in silence | finish blimp document chapter 4 | Have a Pack and Go of designed parts. | Test the feasibility of the data S | 5/15/21 | fill up to here please | Complete dynamic equations with Jacob and Dr. Jiao

8

S | 5/16/21 | Work on Chassis section of report M | 5/17/21 | Start Final presentarion | wrap up Webots simulation | Work on Chassis section of report | Build a physical model and modify the code of the physical model T | 5/18/21 | 0900 Team Meeting | Continue Final Presentarsion outline | wrap up Webots simulation | Work on Chassis section of report | Test the feasibility of the physical model code W | 5/19/21 | Continue Final Presentarsion outline | prepare report on webots simulation | Work on Chassis section of report | Test the feasibility of the physical model code Th | 5/20/21 | 1000 Sponser Meeting | Continue Final Presentarsion outline | Contribute to Final report | Investigate Abaqus FEA | Complete the final webots Blimp simulation F | 5/21/21 | Progress Report | Continue Final Presentarsion outline | Contribute to Final report | Investigate Abaqus FEA | Complete the final webots Blimp simulation S | 5/22/21 | Investigate CFD

9

S | 5/23/21 | Investigate CFD M | 5/24/21 | STATs HW | MTH356 HW | Chassis Implementation T | 5/25/21 | 0900 Team Meeting | Coodinate with team members on Presenation | Modify Blimp | comment code | controls lab | Chassis Implementation | modify Blimp W | 5/26/21 | Presentation: Concept of Operations, Post Mortem | Modify Blimp: | fix blimp only turning CW in correction | controls lab (until noon) Ike Homework | Peer Review Finish | modify Blimp Th | 5/27/21 | 1000 Sponser Meeting | Presentation: Concept of Operations, Post Mortem | Modify Blimp: | implement output of top speed/acceleration/buoyant force/total mass Poster | Poster Work | modify Blimp F | 5/28/21 | Progress Report | Simulations polished | Presentation: Concept of Operations, Post Mortem | Modify Blimp: | Poster | Poster Work | modify Blimp S | 5/29/21 | Presentation: Concept of Operations, Post Mortem | Slide: Demonstrate Webots | Slide: Demonstrate CoppeliaSim | Final project report / philosophy HW | Presentation: Diagram | Documenttation

10
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

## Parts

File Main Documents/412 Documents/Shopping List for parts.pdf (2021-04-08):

Nick’s Blimp Parts Wishlist

- Brain
- Raspberry Pi Pico (https://www.raspberrypi.org/products/raspberry-pi-pico/)
- Length – 51mm
- Width – 21mm
- Height – Thin
- Mass – 19.96g
- Cost - $4.00
- Wireless Comms
- XBee WiFi Module (https://www.digi.com/products/models/xb2b-wfwt-001)
- Length – 32.94mm
- Width – 24.38mm
- Height -
- Mass – Unknown
- Cost - $26.95
- IMU
- Adafruit 9-DOF Absolute Orientation IMU Fusion Breakout (https://www.adafruit.com/product/2472)
- Length – 27mm
- Width – 20mm
- Height – 4mm
- Mass – 18.14g
- Cost – $34.95
- Motors
- Crazepony 8520 Brushed 15000KV Motor (https://www.amazon.com/8-5x20mm-15000KV-Coreless-JST-1-25-Connector/dp/B07CFQMF1M)
- Length – 20mm
- Diameter – 8.5mm
- Mass – 5.2g
- Cost – 16.99 (for 8; 4 CW, 4 CCW)
- ESC
- ESC Brushed Micro 1S 20A Bare Board (https://micronwings.com/Products/ESCBrushedMicro1S20ABareBoard/index.shtml)
- Length – 22mm
- Width – 10mm
- Height – 4.7mm
- Mass – 1.28g
- Cost – $23.40/each (need 3)
- Battery
- FancyWhoop 3.7V 1800mah Lipo Battery 25C (https://www.amazon.com/FancyWhoop-1800mah-Battery-Charger-Quadcopter/dp/B07THZKZ9B)
- Length – 57mm
- Width – 29mm
- Height – 10mm
- Mass – 40.82g
- Cost – $10.99/each

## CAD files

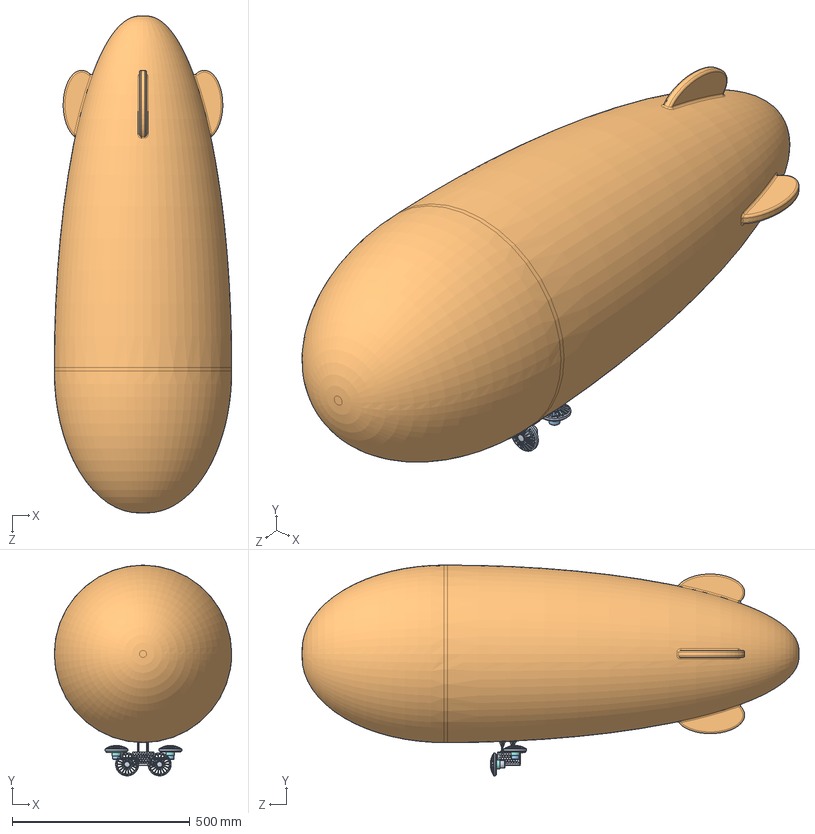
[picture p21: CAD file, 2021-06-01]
Main Documents/Full Blimp Analysis/Full_Assembly_Blimp.SLDASM
500.0 x 593.8 x 1400.0 mm
Cage_V1
Cage_Door
Vertical_Servo_Attachment x 2
92949A315_18-8 SS BUTTON HEAD HEX DRIVE SCREW x 5
90107A005_TYPE 316 STAINLESS STEEL FLAT WASHER x 4
98381A428_ALLOY STEEL DOWEL PIN
Env_Attachment x 2
Bottom_Cage_with_holes (1) x 4
Top_Cage_with_holes x 4
Blimp

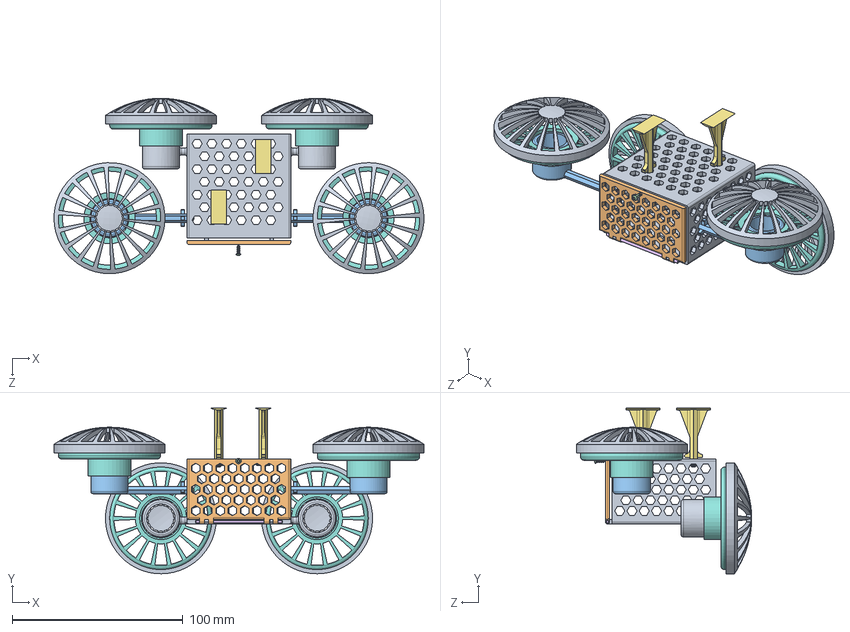
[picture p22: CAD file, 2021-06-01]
Main Documents/Full BOM Assembly/Full_asm.SLDASM
216.7 x 97.0 x 102.7 mm
Cage_V1
Cage_Door
Vertical_Servo_Attachment x 2
92949A315_18-8 SS BUTTON HEAD HEX DRIVE SCREW x 5
90107A005_TYPE 316 STAINLESS STEEL FLAT WASHER x 4
98381A428_ALLOY STEEL DOWEL PIN
Env_Attachment x 2
Bottom_Cage_with_holes (1) x 4
Top_Cage_with_holes x 4

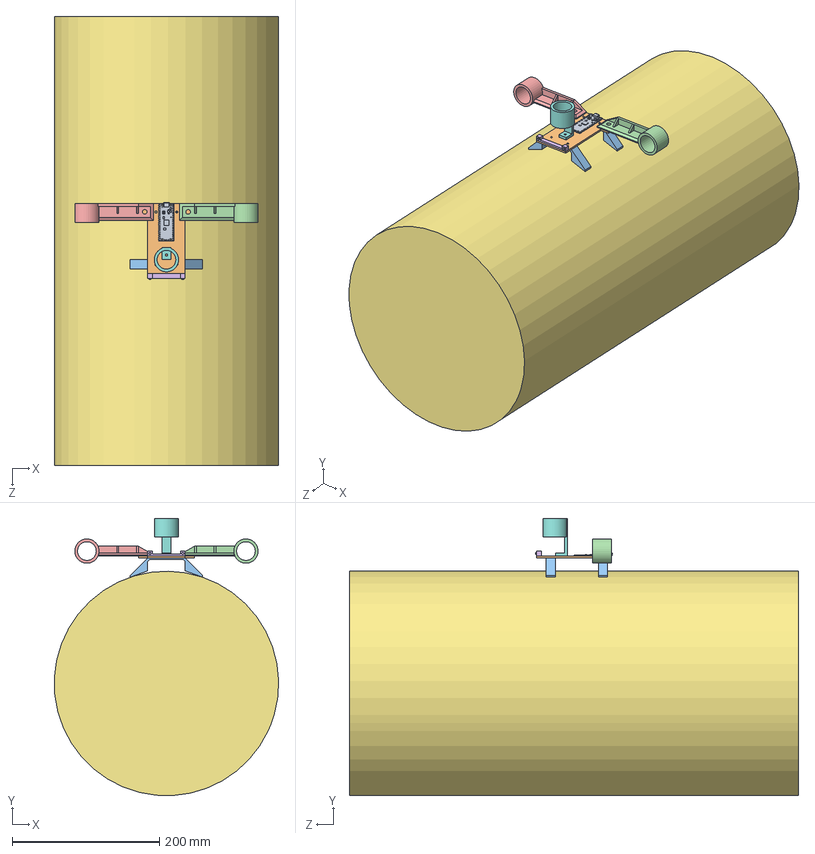
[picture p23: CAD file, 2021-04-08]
Main Documents/413 Documents/Blimp1.0/MainBody.SLDASM
304.5 x 376.1 x 609.6 mm
Pico-R3
MainChassis
AdhesiveMount x 2
MotorMountStarboard
MirrorMotorMountStarboard
MockCamera
MotorMountVertical

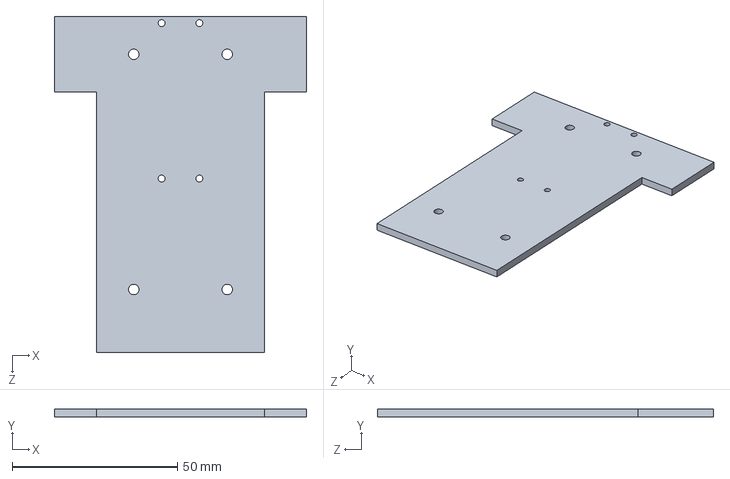
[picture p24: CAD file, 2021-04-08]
Main Documents/413 Documents/Blimp1.0/MainChassis.SLDPRT
76.2 x 2.54 x 101.6 mm

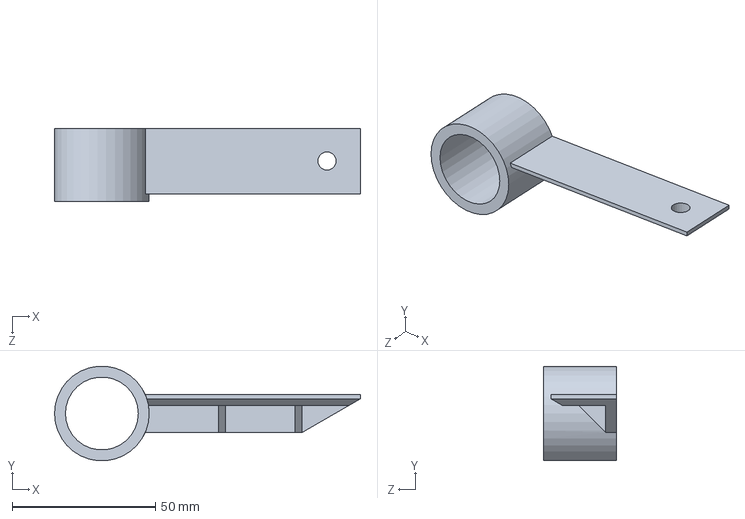
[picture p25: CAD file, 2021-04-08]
Main Documents/413 Documents/Blimp1.0/MotorMountStarboard.SLDPRT
106.7 x 32.9 x 25.4 mm

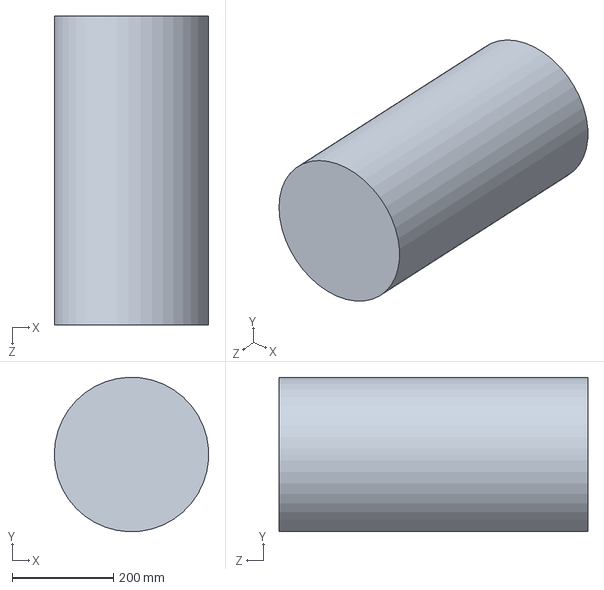
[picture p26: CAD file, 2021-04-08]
Main Documents/413 Documents/Blimp1.0/MockHeEnvelope.SLDPRT
304.8 x 304.6 x 609.6 mm

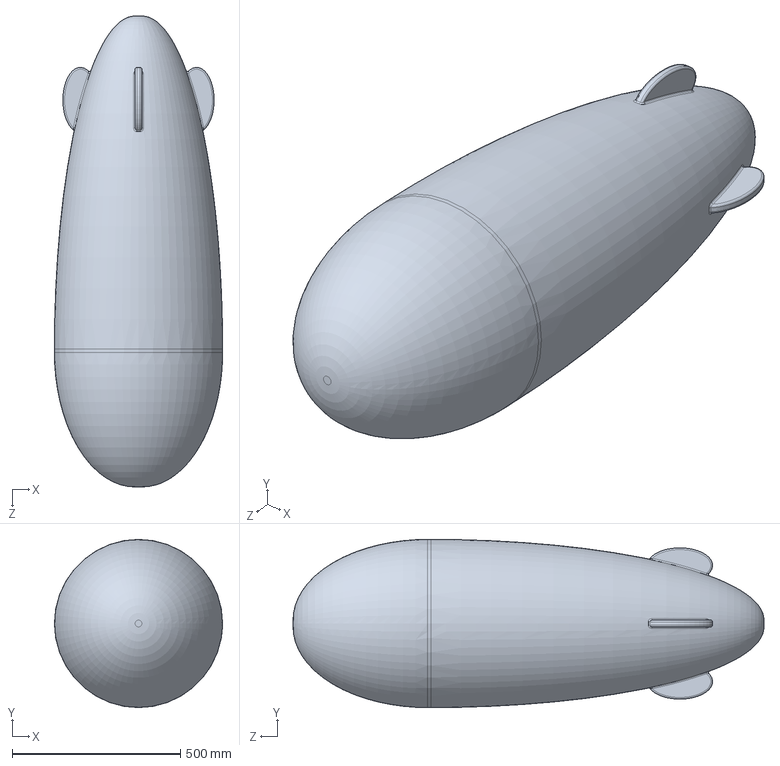
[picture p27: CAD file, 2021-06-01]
Main Documents/Full Blimp Analysis/Blimp.SLDPRT
500.0 x 500.0 x 1400.0 mm

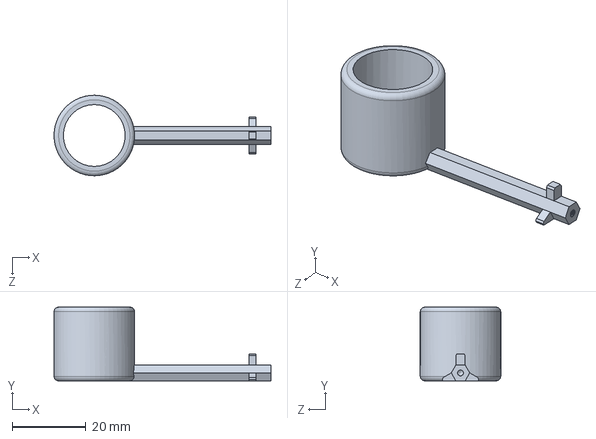
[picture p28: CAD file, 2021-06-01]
Main Documents/Full BOM Assembly/Vertical_Servo_Attachment.SLDPRT
58.8 x 20.0 x 21.8 mm

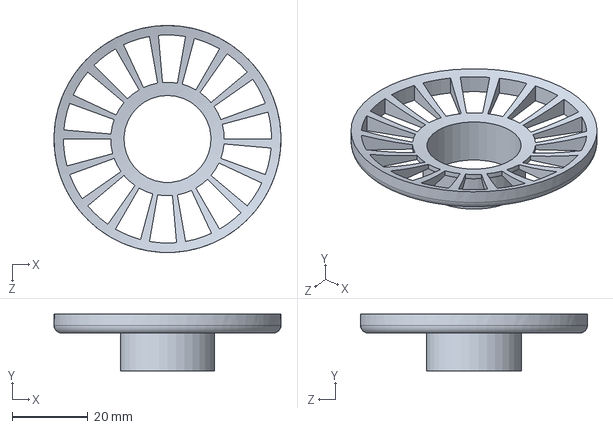
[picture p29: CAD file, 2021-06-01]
Main Documents/Full BOM Assembly/Bottom_Cage_with_holes (1).SLDPRT
60.0 x 15.0 x 60.0 mm

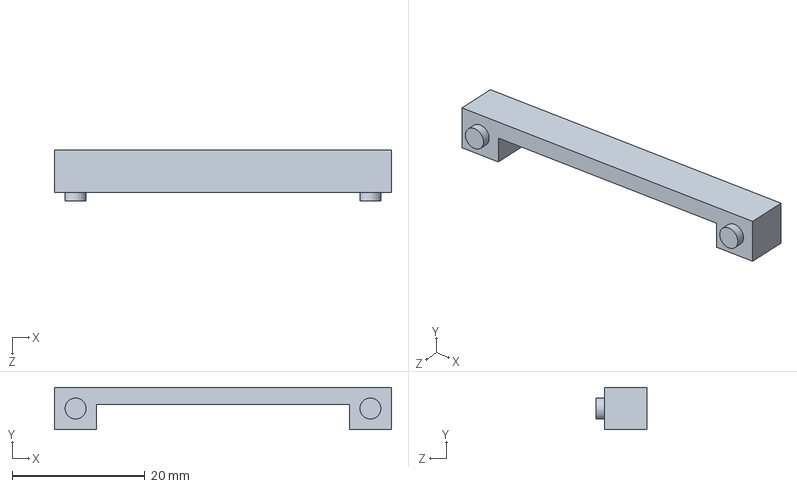
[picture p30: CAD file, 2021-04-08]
Main Documents/413 Documents/Blimp1.0/MockCamera.SLDPRT
50.8 x 6.35 x 7.62 mm

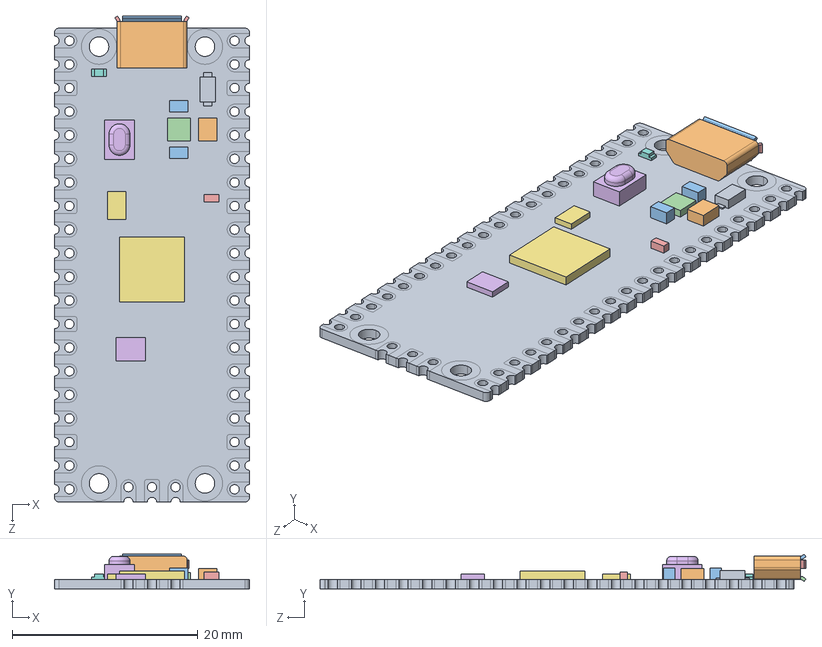
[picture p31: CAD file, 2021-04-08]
Main Documents/413 Documents/Blimp1.0/Pico-R3.step
21.0 x 3.73 x 52.3 mm
PICO_REF_BOARD.STEP
PICO_REF_USB.STEP
PICO_REF_SWITCH.STEP
PICO_REF_MICROCONTROLLER.STEP
PICO_REF_LED.STEP
PICO_REF_ONSEMI.STEP
PICO_BOURNS.STEP
PICO_MURATA.STEP x 2
PICO_RICHTEK.STEP
PICO_DIODES.STEP
PICO_AEL.STEP
PICO_WINBOND.STEP

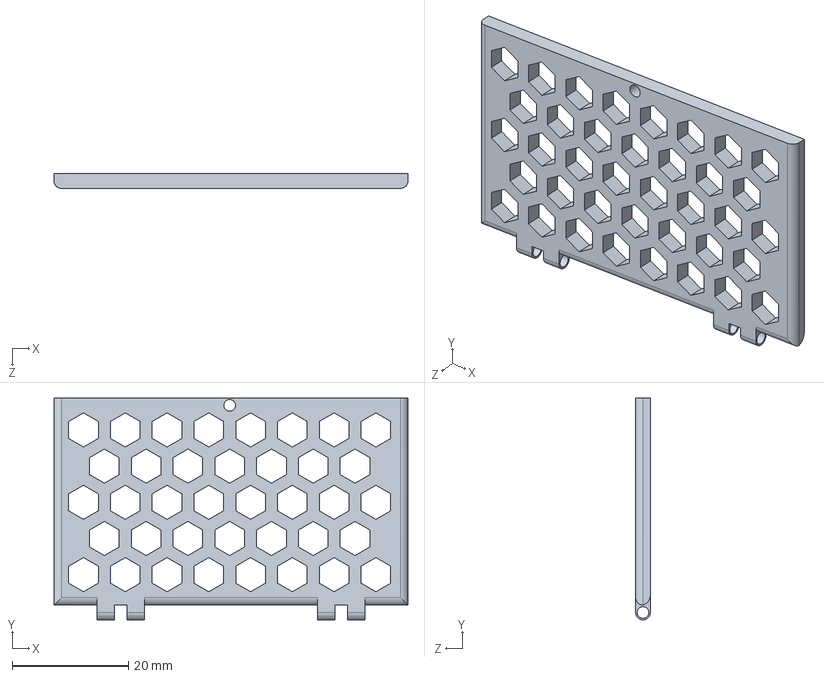
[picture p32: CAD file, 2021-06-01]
Main Documents/Full BOM Assembly/Cage_Door.SLDPRT
60.8 x 38.1 x 2.54 mm

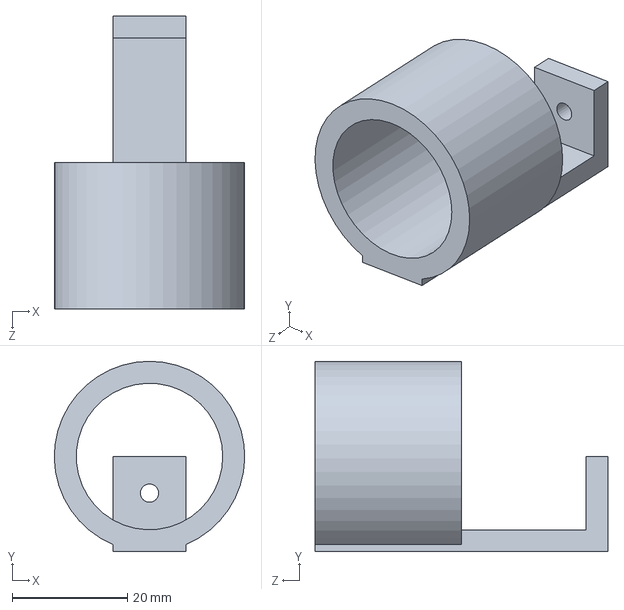
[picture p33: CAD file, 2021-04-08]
Main Documents/413 Documents/Blimp1.0/MotorMountVertical.SLDPRT
33.0 x 33.0 x 50.8 mm

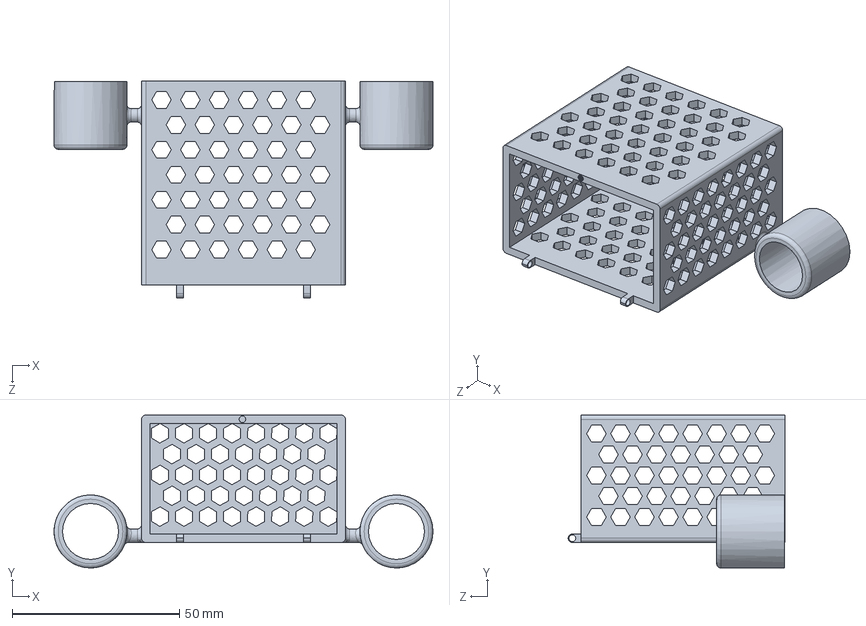
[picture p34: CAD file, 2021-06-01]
Main Documents/Full BOM Assembly/Cage_V1.SLDPRT
113.3 x 45.7 x 64.8 mm

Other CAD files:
Main Documents/413 Documents/Blimp1.0/MirrorMotorMountStarboard.SLDPRT
Main Documents/Full BOM Assembly/Env_Attachment.SLDPRT
Main Documents/413 Documents/Blimp1.0/AdhesiveMount.SLDPRT
Main Documents/Full BOM Assembly/Top_Cage_with_holes.SLDPRT
Main Documents/413 Documents/Blimp1.0/Pico-R3.SLDPRT
Main Documents/Full BOM Assembly/90107A005_TYPE 316 STAINLESS STEEL FLAT WASHER.SLDPRT
Main Documents/Full BOM Assembly/92949A315_18-8 SS BUTTON HEAD HEX DRIVE SCREW.SLDPRT
Main Documents/Full BOM Assembly/98381A428_ALLOY STEEL DOWEL PIN.SLDPRT

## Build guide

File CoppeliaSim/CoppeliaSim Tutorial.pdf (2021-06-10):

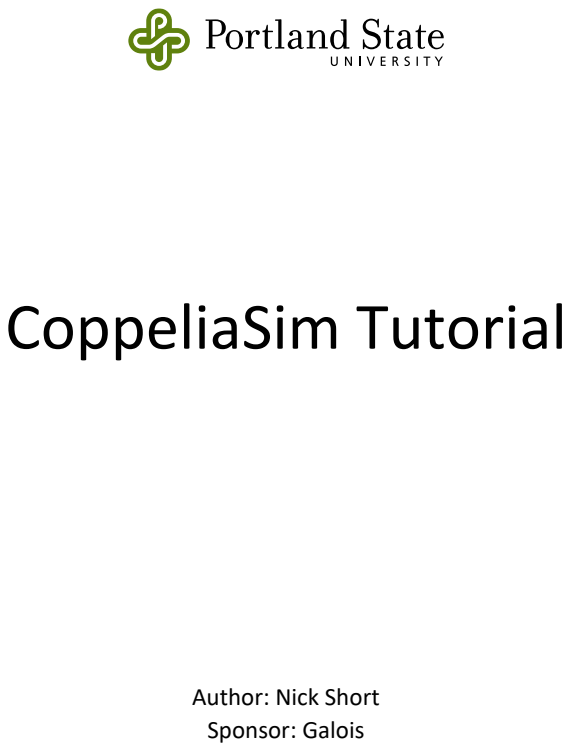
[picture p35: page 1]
CoppeliaSim Tutorial

Author: Nick Short
Sponsor: Galois

## Table of Contents

## Introduction

This document serves as a basic tutorial for Coppelia Robotics’ simulation suite, CoppeliaSim. This document was created as part of a Portland State University ECE/ME Capstone project sponsored by Galois. Dr. Marek Perkowski oversaw this project as the faculty advisor.

## Scope

This tutorial will cover the basics of the simulation software, including an overview of the environment, menu options, and advanced dialogue boxes. Also included will be instructions on creating objects, attaching and configuring scripts, and hierarchical organization of objects.

Finally, there will be a section covering a selection of useful API functions built into the CoppeliaSim environment, as well as some of the pitfalls experienced during the creation of the Capstone project, as related to the simulation software.

## Acknowledgements

I would like to recognize the other members of my Capstone team for shouldering the burden of basically every aspect of this project that did not revolve around CoppeliaSim. A hearty thanks to:

- Ben
- Jacob
- Victor
- Zeming
- Dylan

A special thanks to Jacob for his assistance with much of the control dynamics of the simulations.

I would also like to thank Dr. Marek Perkowski for advising on this project, as well as Dr. Mark Faust and Andrew Greenberg for their guidance during this project.

Finally, I would like to thank our sponsor’s representative, Ethan for his supreme patience as this project metamorphized from what we thought it would be to what it became.

## Environment

The following pages contain images and explanations of the various sections of the CoppeliaSim environment.

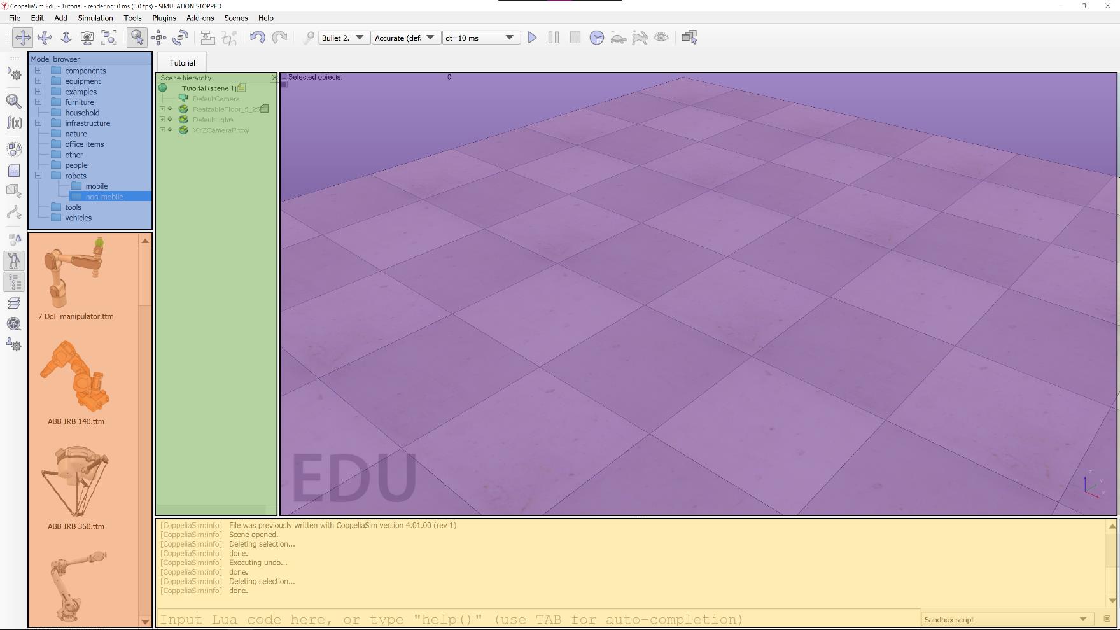
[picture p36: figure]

Figure 1 - CoppeliaSim environment

Figure 1 shows the CoppeliaSim environment, divided into functional sections. The blue section is the Model browser where the user can select from many different prefab models to insert into the simulation. The orange section is a visual list of the options available in the current selection of the Model browser. The green section is the Scene hierarchy—the list of all objects in the scene, respecting parent/child relationships. The purple section is the scene visualization. This is where the simulation plays out, and where the user can manually move objects around. The yellow section is the script output and (if enabled) the Lua Commander interface (Lua Commander will be discussed later). Information displayed using the Lua print function will be displayed here.

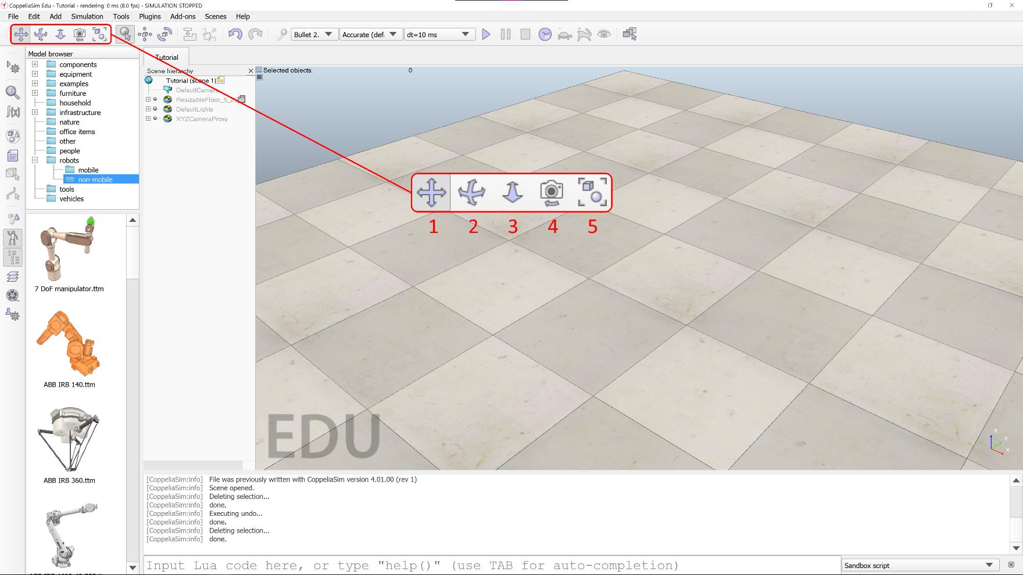
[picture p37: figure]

Figure 2 - Camera buttons

### Toolbar Buttons – Camera

Figure 2 shows the camera view manipulation operations, as described below:

1. Translate – Move the camera view along the X-Y-Z axes.
2. Rotate – Rotate the camera view about the X-Y-Z axes.
3. Zoom – Zoom in and out. Function appears to be identical in orthogonal and perspective projection modes.
4. Camera Angle – In perspective projection mode, adjusts the projection angle of the camera. In orthogonal projection mode, acts as the zoom mode.
5. Fit-to-view – Fits the selected objects within a large portion of the scene view. If no items are selected, attempts to fit all objects within the view.

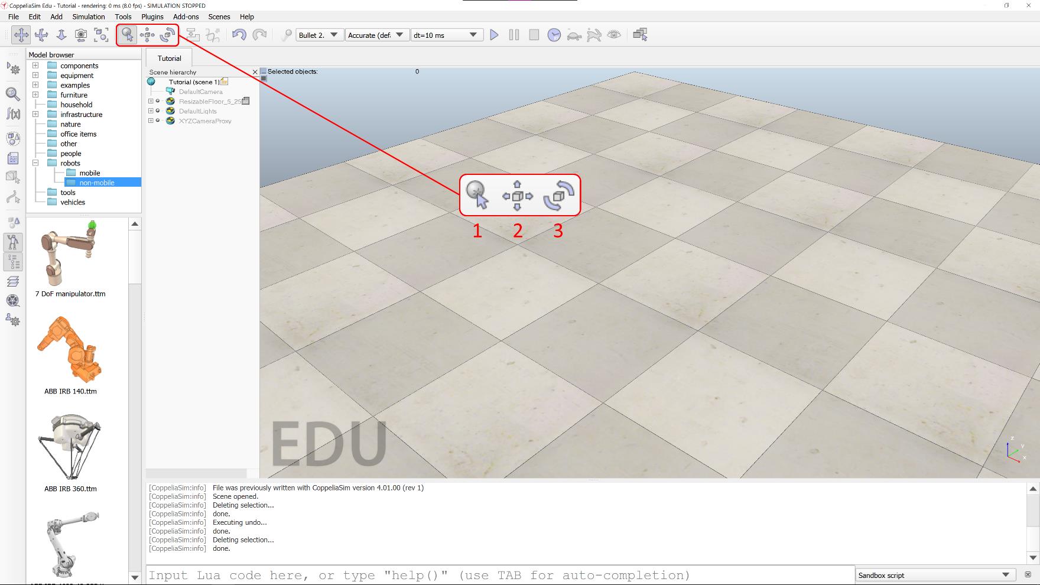
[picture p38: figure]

Figure 3 – Selection and object manipulation buttons

### Toolbar Buttons – Selection and Object Manipulation

Figure 3 shows the buttons used to select an object and manipulate its position and orientation, as described below:

1. Object selection – Selects an object.
2. Object translation – Opens the object translation dialog box, allowing an object to be translated along one or more axes.
3. Object rotation – Opens the object rotation dialog box, allowing an object to be rotated around one or more axes.

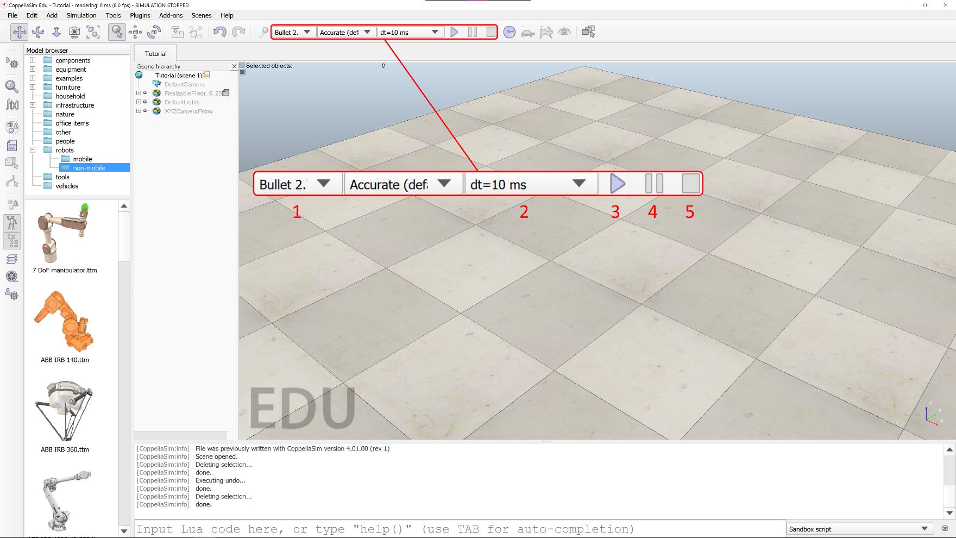
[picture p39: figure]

Figure 4 - Simulation buttons

### Toolbar Buttons – Simulation

Figure 4 shows the buttons/drop downs used to change some parameters related to the simulation execution, as described below:

1. Physics engine – This drop down allows the user to select the desired physics engine. Available options are Bullet 2.78, Bullet 2.83, ODE, Vortex, and Newton.
2. Simulation time step – This drop down allows the user to select the amount of time that passes between simulation frames.
3. Start simulation – Starts the simulation.
4. Pause simulation – Pauses the simulation.
5. Stop simulation – Stops the simulation.

## Menus

The following pages contain images and explanations of the various menus available in the CoppeliaSim environment.

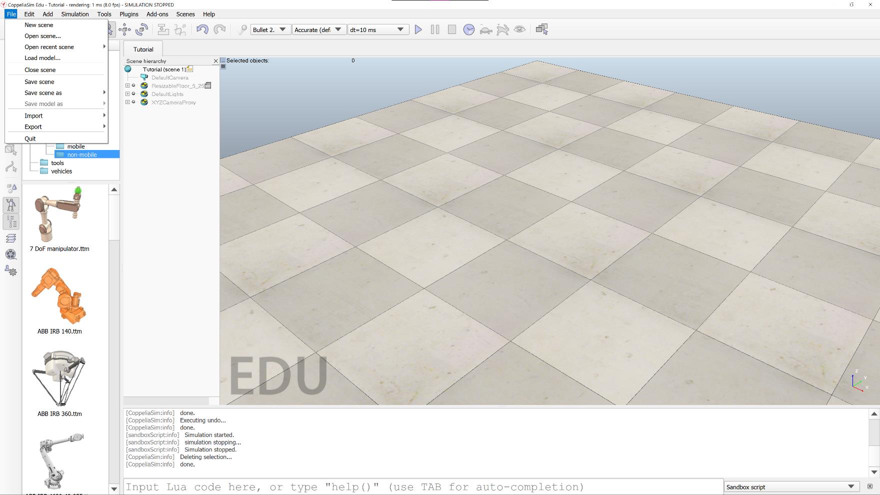
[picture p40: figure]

Figure 5 - File Menu

### File

This is a standard file menu. It gives the user the option to create a new scene, save an open scene (or save a copy using “Save scene as”) and open a saved scene. The Import, Export, and Load model… options are also helpful, particularly Import. With the Import function, the user can add a custom complex shape (as a mesh) to a scene using a .dxf or .stl file, exported from the 3D modeling software of their choice. A list of recently opened scenes can also be found, allowing for quick access.

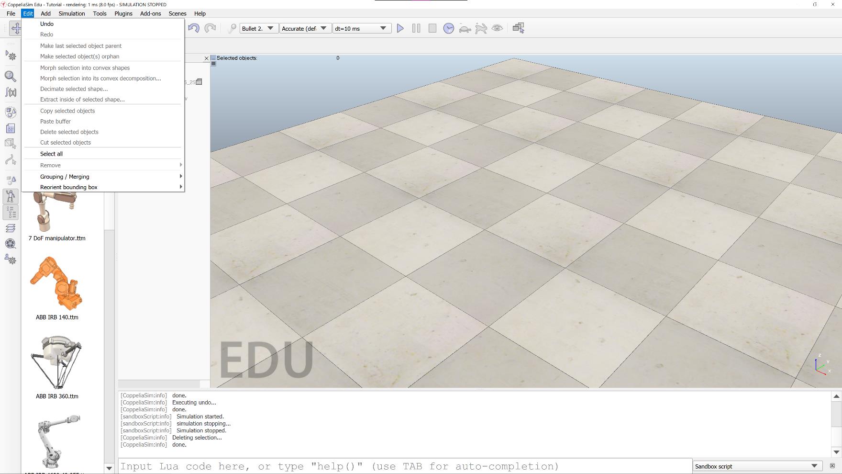
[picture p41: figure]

Figure 6 - Edit Menu

### Edit

The edit menu has some standard edit menu options. Undo/Redo, Select All, and Copy/Cut/Paste have their normal uses. Make last selected object parent, when selecting multiple objects, makes the last object selected the parent object of the other selected objects. Make selected object(s) orphan causes all selected objects to have no child relationship with any other. Grouping / Merging allows the user to “combine” multiple objects into a single shape that can be translated, rotated, and otherwise utilized together. Reorient bounding box alters the rotation of the objects bounding box to be aligned with a different reference frame, usually the world reference frame.

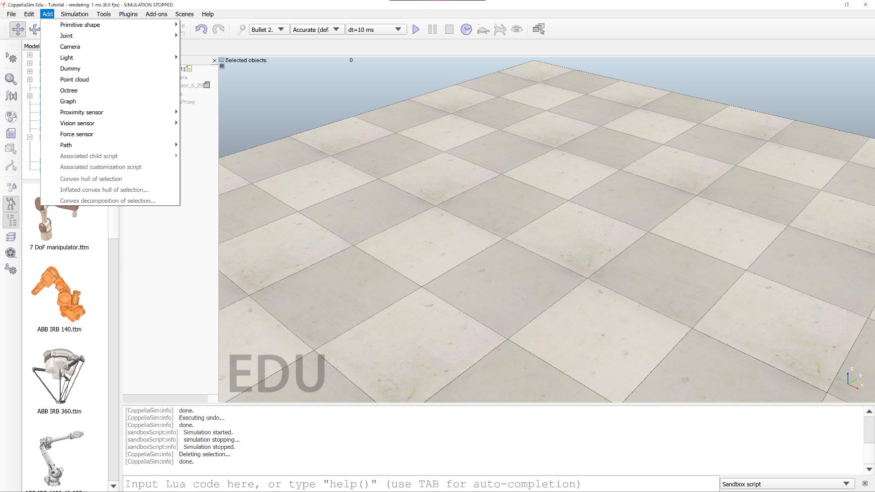
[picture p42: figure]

Figure 7 - Add Menu

### Add

As the name suggests, the Add menu allows the user to add entities to the scene. Covered in this tutorial will be Primitive Shape, Joint, and Associated child script. For information on the addition entities that CoppeliaSim provides, please refer to the CoppeliaSim documentation, a link to which can be found at the end of this document.

Primitive shapes available include: Planes, Discs, Cuboids, Spheres, and Cylinders. Available joints include: Revolute, Prismatic, and Spherical.

Child scripts can be either threaded, or non-threaded.

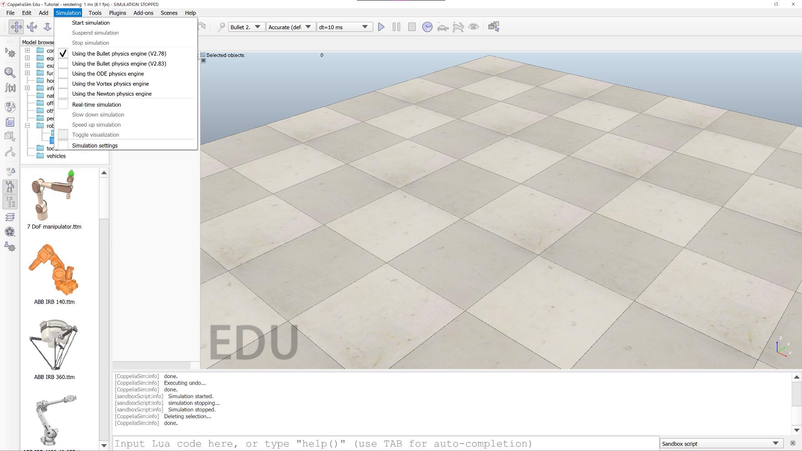
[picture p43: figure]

Figure 8 - Simulation Menu

### Simulation

The simulation menu allows the user to start, pause, or stop the simulation, as well as select the desired physics engine. Also available are options to run a Real-time simulation, Speed up and Slow down the simulations, and open the Simulation settings.

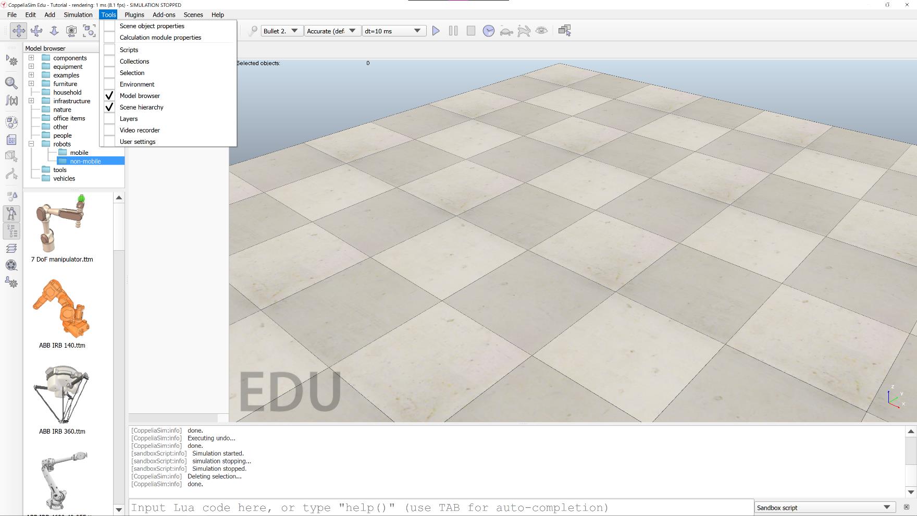
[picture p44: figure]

Figure 9 - Tools Menu

### Tools

This menu gives the user the option of opening several different side-panes and advanced dialog boxes. Of note are the Model browser and Scene hierarchy, which are enabled by default in a new scene. Discussed later in this tutorial will be the Scene object properties, Scripts, and User settings advanced dialog boxes.

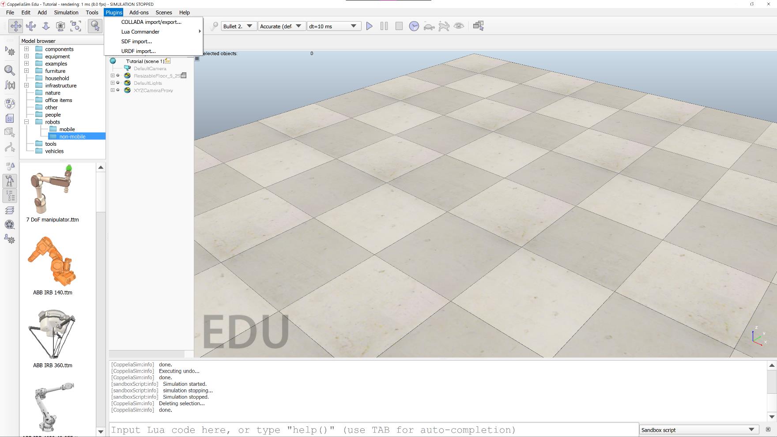
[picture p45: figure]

Figure 10 - Plugins Menu

### Plugins

The only option in this menu addressed in this tutorial is Lua Commander. Entering the Lua Commander sub-menu and selecting Enable will allow the user to “inject” Lua commands—including functions included in the CoppeliaSim API—into the simulation during runtime. This feature allows the user to change many simulation runtime parameters, as well as user-defined signals (global variables). These commands are executed right after the last line executed in whichever script is being executed when the command is given to Lua Commander.

The utility of this plugin as a way to monitor signals in state-based simulations will be discussed in a later section.

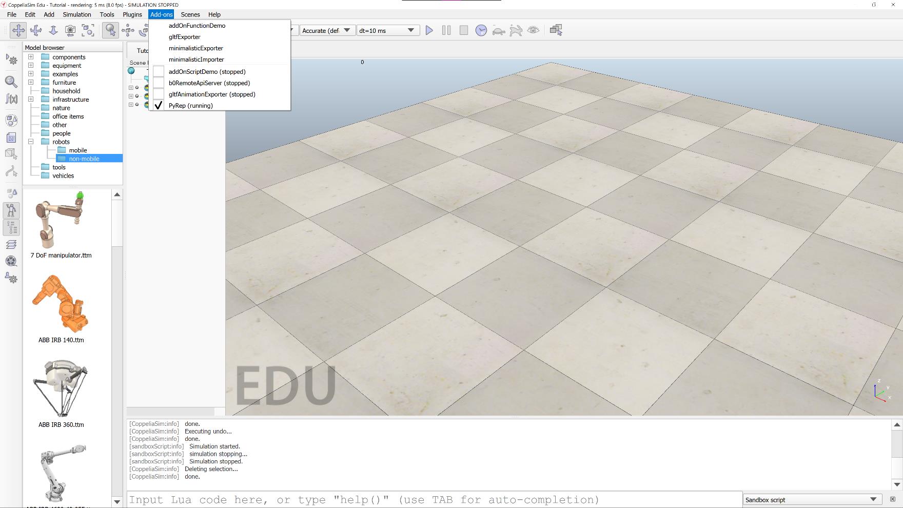
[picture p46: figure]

Figure 11 - Add-ons Menu

### Add-ons

The PyRep add-on allows the user to control CoppeliaSim directly with Python. The creators of PyRep modified the open-source version of CoppeliaSim to eliminate the communication delays associated with remote API access (notably, the socket and interthread communication delays). This results in an approximate four orders of magnitude speed increase over the standard remote API access.

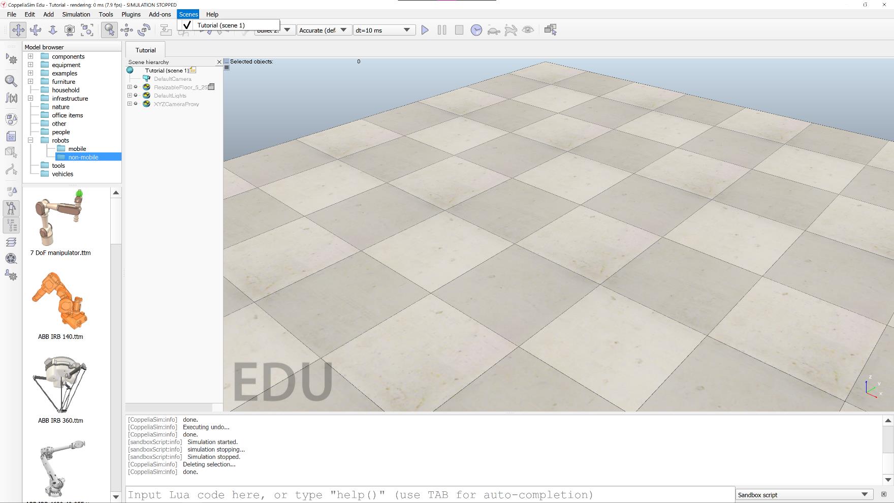
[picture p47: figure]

Figure 12 - Scenes Menu

### Scenes

This menu is equivalent to a standard “Windows” menu, allowing the user to switch between active and inactive (but loaded) simulations.

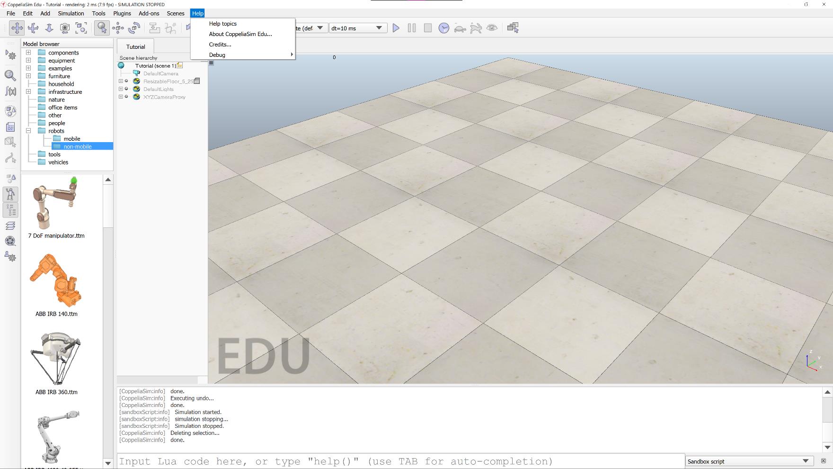
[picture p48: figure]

Figure 13 - Help Menu

### Help

The Help options selection in the Help menu directs the user to the CoppeliaSim User Manual website. This manual contains explanations of the features and functions of CoppeliaSim, basic and advanced tutorials, and the complete CoppeliaSim API (including the remote API), among others.

## First Steps

In this section, we will cover the basics of adding a primitive shape to a scene and looking at the Geometry and Dynamic Properties dialog boxes.

### Adding a Shape to a Scene

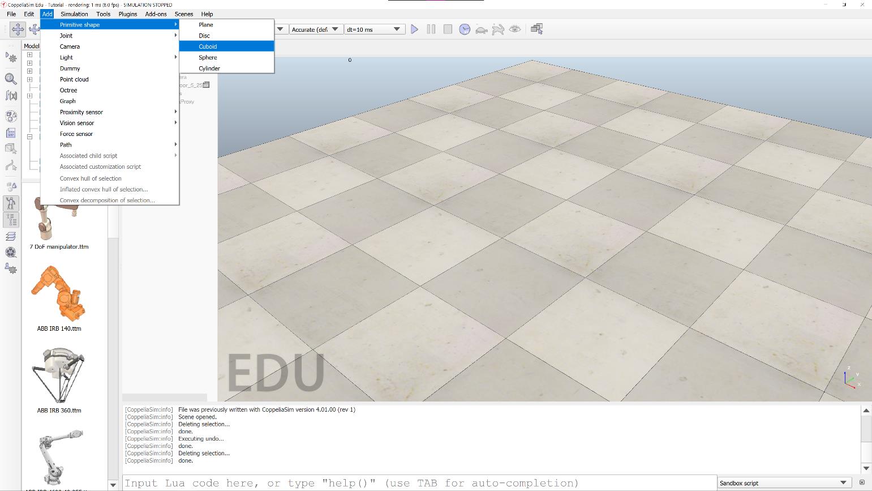
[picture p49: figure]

Figure 14 - Adding a shape to a scene

As shown in Figure 14, clicking through Add->Primitive shape->Cuboid will allow us to add a Cuboid shape to the scene. Upon clicking Cuboid, you will see the following dialog box, shown in Figure 15.

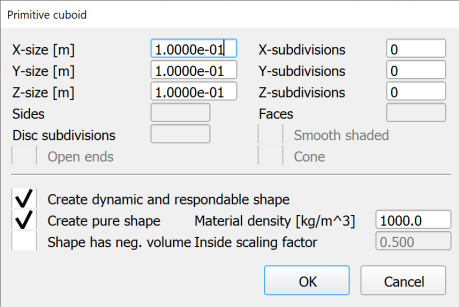
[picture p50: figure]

Figure 15 - Add primitive shape dialog box (cuboid)

In this dialog box, the dimensions and density of the new primitive shape can be configured. The shape can also be configured as a dynamic and respondable shape, allowing it to be affected by the physics engine, and to collide with other objects.

### Modifying a Shape’s Geometry and Dynamic Properties

A shape’s geometry and dynamic properties can be modified post creation, through the appropriate dialog box. First, double-click on the shape’s symbol (the blue cube, in this case) in the hierarchical tree, as shown in Figure 16.

Figure 16 - Opening shape properties

After double-clicking on the shape’s symbol, the dialog box in Figure 17 will be shown.

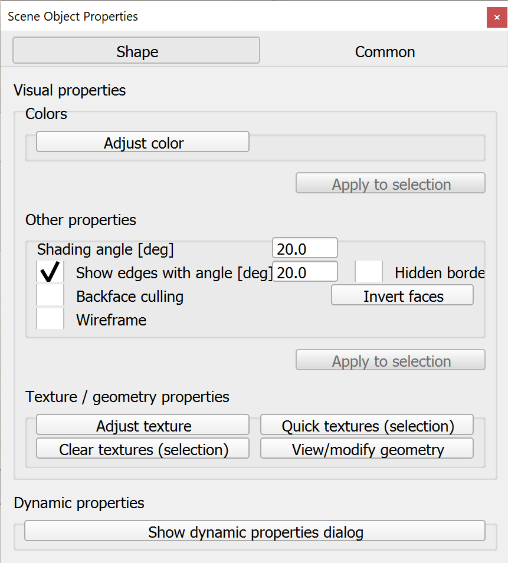
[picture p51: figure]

Figure 17 - Object properties

From this dialog box, the user has access to the geometry and dynamic properties dialog boxes.

Figure 18 shows the Geometry associated with ‘shape’ dialog box (here, for a cuboid).

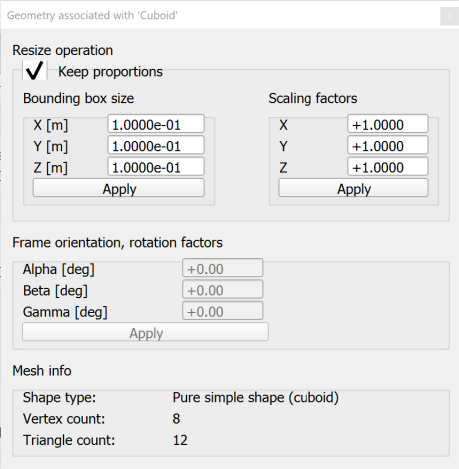
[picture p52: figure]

Figure 18 - Object geometry dialog box

This dialog allows the user to adjust the dimensions of a shape, either by setting a dimension to an absolute size, or by scaling the dimension by a factor. By default, the Keep proportions option is selected and the other dimensions will be scaled by a factor similar to how the altered dimension is scaled.

Figure 19 shows the Rigid Body Dynamic Properties dialog box. It is recommended that the user only alter whether or not the object is respondable or dynamic, as changing the settings below the Body is dynamic checkbox can drastically affect the simulation (Principle moments of inertia and position/orientation of the inertial frame are all calculated at shape creation, using the shape’s dimensions and mass. Mismatches between mass and inertial moments can cause odd things during simulaion.)

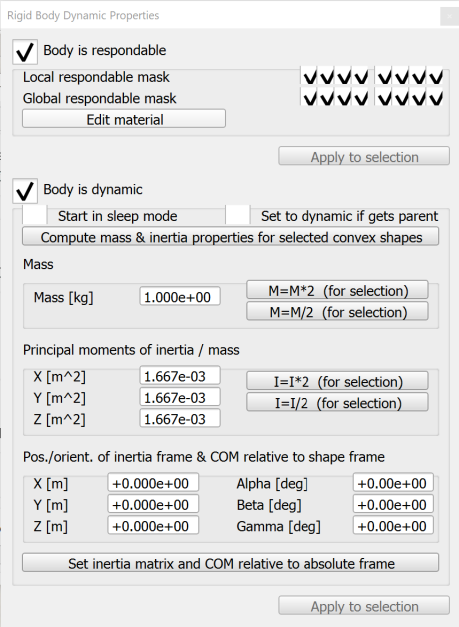
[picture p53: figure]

Figure 19 - Shape dynamic properties dialog box

### Manipulating a Shape’s Position and Orientation

The position and orientation of a shape can be adjusted precisely with a few different methods. Figures 20 through 22 show the various options available for shape translation.

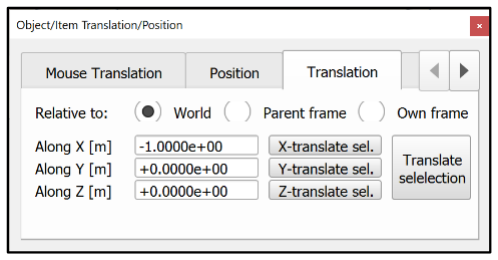
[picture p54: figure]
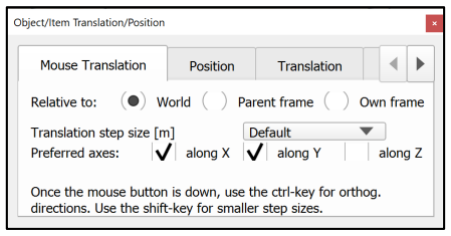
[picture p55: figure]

Figure 20 - Mouse translation | Figure 21 – Specific position | Figure 22 - Exact translation along axes

Mouse translation allows the user to drag a shape around the scene. The user can “lock” axes by deselecting them. With specific position, the user can specify the exact location of a shape in X-Y-Z, relative to the world, or the parent frame. This is useful for centering a child object on a parent object in one or more axes (to center on a parent, the coordinate would just be set to 0). Exact translation allows the user to “slide” a shape along one or more axes by a specific amount.

Figures 23 through 26 show the various options for shape rotation.

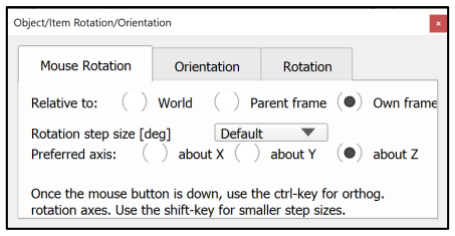
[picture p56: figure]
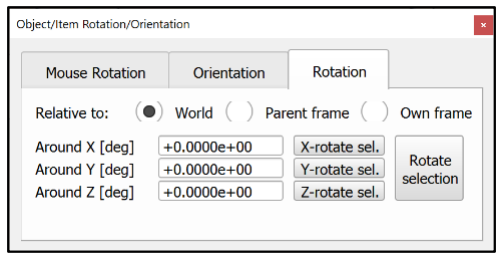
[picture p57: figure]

Figure 23 - Mouse rotation | Figure 24 – Specific rotation | Figure 25 - Exact rotation about axes

Mouse rotation allows the user to freely rotate a shape about an axis using the mouse. Specific rotation allows the user to rotate a shape to a specific angle, relative to the world, or the parent frame. This is useful for equalizing the rotation between parent-child objects. Exact rotation about an axis allows the user to rotate a shape about one or more axes by a specific amount.

### Joints

In CoppeliaSim, joints are what hold objects together. There are three types of joints: revolute, prismatic, and spherical.

- Revolute – These joints allow one shape to rotate with respect to another shape.
- Prismatic – These joints allow one shape to extend or retract from another shape. A linear actuator is an example of this.
- Spherical – These joints allow one shape to rotate in three dimensions about another shape.

Joints have three modes of operation: passive, dependent, and torque/force. The passive mode is the only mode used in this basic tutorial. In passive mode, a joint connects two objects together and the joint position can be controlled through the API.

## Scripts

Scripts are an integral part of CoppeliaSim simulations. They control pretty much everything aside from the application of the physics engine. Scripts are written in Lua, using CoppeliaSim’s API functions, which all follow the format sim.someFunctionInCoppeliaSIM(arg1, arg2, …). In addition to CoppeliaSim’s API functions, all base Lua functions (for Lua version 5.1) are available, as well as some extended libraries, like string and math.

Scripts in CoppeliaSim are attached to shapes or other objects and have a configurable execution order, largely based upon the parent-child hierarchy of the scene. Scripts are not accessible to external editors, as they are stored in the simulation .ttt file. Scripts are not always required to be attached to shapes or other objects, though. Through the Lua function require(path), the user can execute external scripts within an integrated script.

The user can define their own functions to perform often repeated actions, or even to expand upon existing CoppeliaSim API functions (often referred to as ‘wrapping’). All user-defined functions must be called within one of the built-in state functions, or they will not execute.

### Script Types

There are two types of scripts: child and customization. Additionally, child scripts can either threaded or non-threaded.

- Child – These scripts are executed each simulation pass (so, only when the simulation is running), in parts (aside from the sysCall_init() function, which is called at the beginning of the simulation, and only once).
- Threaded – Threaded scripts are not covered in this tutorial. They are useful for some things, but carry a hefty thread-switching overhead which can quickly make simulations choppy and unresponsive.
- Non-threaded – Non-threaded scripts must be non-blocking, meaning that they should always return control to the system (e.g. no wait loops).
- Customization – Customization scripts run all the time, whether a simulation is started or stopped. These scripts are useful, especially when combined with a remote API connection. For example, a GUI could be designed in Python to allow the live scaling of an object’s bounding box.

There are four main built-in state functions for child scripts: sysCall_init(), sysCall_actuation(), sysCall_sensing(), and sysCall_cleanup(). All sysCall_init() functions are executed at the start of a simulation. All sysCall_actuation() functions are executed during the actuation stage of a simulation frame. Likewise, all sysCall_sensing() functions are executed during the sensing stage of a simulation frame. The sysCall_cleanup() functions are called at the end of a simulation.

Customization scripts have three built-in state functions (in addition to init and cleanup, which function the same as in child scripts): sysCall_nonSimulation(), sysCall_beforeSimulation(), and sysCall_afterSimulation(). sysCall_nonSimulation() runs constantly when the simulation is not running. sysCall_beforeSimulation() runs just before a simulation starts, and sysCall_afterSimulation() runs just before a simulation ends.

### Adding a Script to a Shape

Figure 26 shows how to add a script to a selected shape or object using the Add menu: Add->Associated child script->Non threaded. This option is only highlighted when a shape or object is selected.

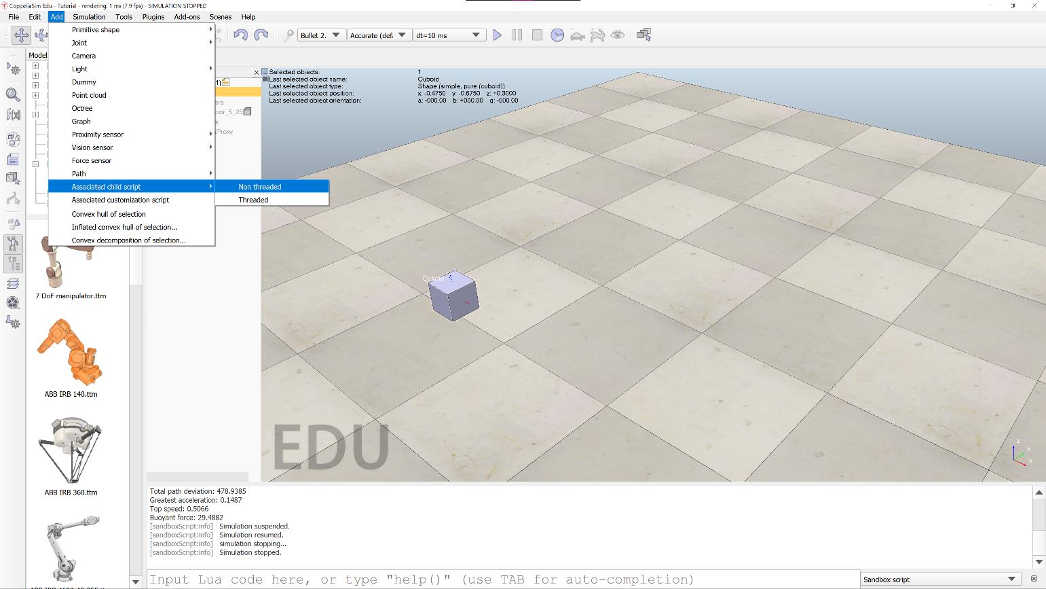
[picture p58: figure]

Figure 26 - Adding a script to a shape

## API

This section will cover some common CoppeliaSim API calls and will address some caveats associated with them (as necessary). There will be a couple of suggestions for custom functions that implement a functionality similar to an API call, where the API call returns an unintuitive, but similar value.

### Common API Calls

The following is a list of common API calls (not included, but required is a sim. prefix):

- getObjectHandle(string objectName) – This API call returns the integer handle of the object named objectName.
- getObjectOrientation(int objectID, int relativeTo) – This API call returns a three member table containing the rotation (in radians) matrix of the object with handle objectID, relative to the object with handle relativeTo.
- If -1 is passed as relativeTo, the orientation is returned relative to the world.
- The angles returned are the Euler angles, different than what one would commonly consider a rotation angle.
- getObjectPosition(int objectID, int relativeTo) – This API call returns a three member table containing the position (in meters) matrix of the object with handle objectID, relative to the object with handle relativeTo.
- If -1 is passed as relativeTo, the position is returned relative to the world.
- getObjectVelocity(int objectID) – This API call returns two three member tables.
- The first table contains the objects linear velocities (units of m/s) in x, y, and z.
- The second table contains the objects angular velocities (units of rad/s) in x, y, and z.
- The radians in the angular velocity table are Euler angles.
- alphaBetaGammaToYawPitchRoll(float alpha, float beta, float gamma) – This API function converts alpha-beta-gamma angles to yaw-pitch-roll angles.
- It returns three separate float values—yaw first, then pitch, and, finally, roll.
- checkDistance(int objectID1, int objectID2, float threshold) – This API call returns the minimum distance between the bounding boxes of the two objects (or collections of objects).
- objectID1 and objectID2 can be the integer handles for individual objects, object collections, or any combination of those. The threshold determines whether the distance is returned. If the distance is greater than the threshold, the distance is not returned. If threshold is ≤0, then no threshold is used.
- The call returns three values.
1. The success of the call (0 if failed, 1 if no threshold or distance is smaller than threshold).
2. A seven-member table of floats, where members 1-6 represent the distance segment. The last member is the minimum distance.
3. A tuple containing the integer handles of the two objects with the minimum distance.
- See caveats.
- addForceAndTorque(int objectID, table3 forces, table3 torques) – This API call is the main interaction with the physics engine. It applies a 3-dimensional force vector and torques about each axis to the object with handle objectID.
- setIntegerSignal(string signalName, int value) – This API call sets an integer signal with name signalName to a specific value.

- getIntegerSignal(string signalName) – This API call retrieves the value of the integer signal with name signalName

Note: There are getXSignal and setXSignal API calls for many of the variable types in Lua. See the CoppeliaSim API reference for a complete list.

### Caveats

The use of some functions in CoppeliaSim may not be intuitive, or the functions may return values that may differ from what you expect. The best example of this is:

sim.checkDistance(int objectID1, int objectID2, float threshold)

If one has a habit of forgetting that CoppeliaSim is a physics-based robotics simulator, one might think that this API call returns just the distance between the two objects center points. One might think, though, that collision detection is a common need in physics simulation. Then, one might remember that this API call returns the minimum distance between objects.

One might also forget that this function returns multiple values (counter-intuitive if one is just expecting a distance). This memory lapse would result in all distance measurements being equal to one, which is obviously broken, but does not error.

In Lua, when functions return multiple values, assignment is like Python, except that “uncaught” return values are discarded in Lua, rather than converted into a tuple, as in Python. As an example, the proper use of the above API call is:

success, distances, objectPair = sim.checkDistance(int objectID1, int objectID2, -1)

The value of success would be 1, distances would be a table[7], and objectPair would be a table[2]. If, instead, the following command was executed:

success = sim.checkDistance(int objectID1, int objectID2, -1)

The value of success would be 1. In Python, the value of success would be:

(1, [val1, val2, … , val7], [handle1, handle2])

The other caveat that is important to mention is that API calls that return angles return the Euler angles (alpha, beta, gamma), not the angles that most people are used to (yaw, pitch, and roll). The only exception to this is the API call that converts from alpha/beta/gamma to yaw/pitch/roll values.

Manual calculations on Euler angles will not work as expected, so they should be converted before use.

## Additional Resources

CoppeliaSim Online Reference Manual – https://www.coppeliarobotics.com/helpFiles/

PyRep Github Repository – https://github.com/stepjam/PyRep

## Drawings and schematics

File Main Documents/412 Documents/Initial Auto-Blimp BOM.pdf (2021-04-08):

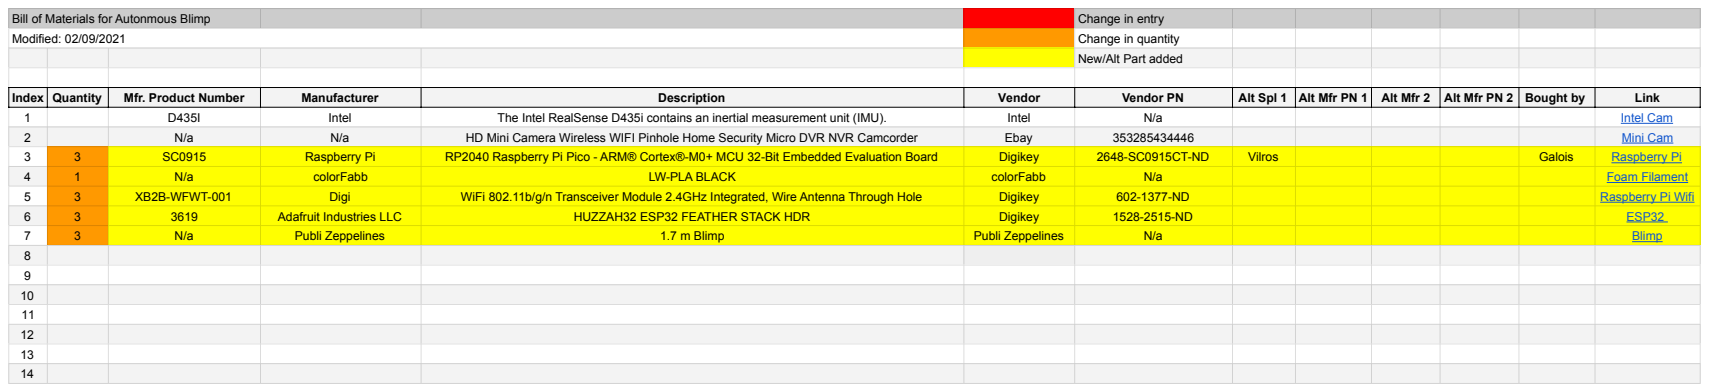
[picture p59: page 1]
Bill of Materials for Autonmous Blimp; Change in entry Modified: 02/09/2021; Change in quantity; Index; Quantity; Mfr. Product Number; Manufacturer; Description; Vendor; Vendor PN; Alt Spl 1; Alt Mfr PN 1; Alt Mfr 2; Alt Mfr PN 2; Bought by; Link; Intel; The Intel RealSense D435i contains an inertial measurement unit (IMU).; Intel Cam; HD Mini Camera Wireless WIFI Pinhole Home Security Micro DVR NVR Camcorder; Ebay; Mini Cam; Raspberry Pi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

New/Alt Part added
